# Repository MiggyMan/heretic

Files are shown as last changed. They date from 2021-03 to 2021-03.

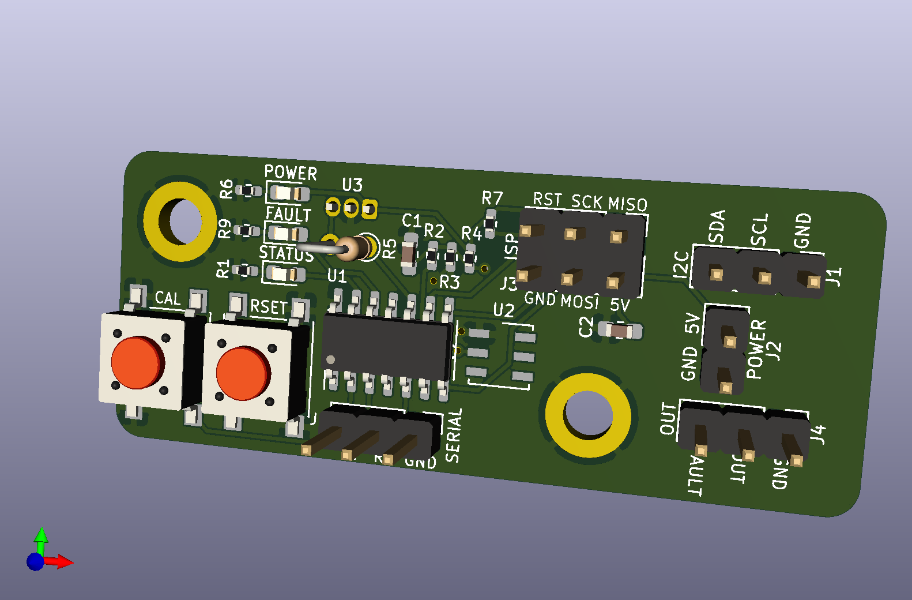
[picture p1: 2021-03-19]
electrical/kicad/filaSens-attiny84.png

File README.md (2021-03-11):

# heretic

My take on the infidel sensor

Forked from https://github.com/drspangle/infidel-sensor

# Original readme below

# Inline Filament Diameter Estimator, Lowcost (InFiDEL)

<p xmlns:dct="http://purl.org/dc/terms/" xmlns:vcard="http://www.w3.org/2001/vcard-rdf/3.0#">
  <a rel="license"
     href="http://creativecommons.org/publicdomain/zero/1.0/">
    
  </a>
  Originally created by Thomas Sanladerer
</p>

*A cheap, yet precise filament diameter sensor, intended to compensate for filament diameter deviations in real-time.*

The InFiDEL is a cheap (< $5) filament diameter sensor intended for use with FDM 3d printers.
The sensor can be calibrated to provide surprisingly precise filament diameter readings in real-time. 
The main idea is to use the sensor to correct for filament diameter deviations while printing.

Based on this proof-of-concept: https://www.youmagine.com/designs/filament-diameter-sensor

## Assembly and Setup
Assembly and Setup Instructions on Youtube (https://www.youtube.com/watch?v=RYgdLPe_T0c)

### Calibration
- Flash board with calibration.ino
- Connect a host via I2C (see provided host-example.ino)
- Insert each calibration drill bit shafts and replace the lookup table entries in driver.ino with your own measurements
  * Measure the actual diameter of the shafts and fill second column
  * Use the host's output *1000 to fill first column
- Finally, flash driver.ino with your values filled out
- Hub should now output exact diameter values

#### Note:
Analog output is currently not enabled in driver.ino (I2C and FAULT pin only)

## BOM

### Printed Parts
1 Block
1 Lever

#### Note:
Parts should preferably be printed in PETG, ABS or ASA as PLA may creep significantly over time.

### Electronics
There are two board variants included in this repository, either can be used to assemble the InFiDEL.

Choose one:
- SMT control board (which is populated; Gerber files and component specifications are included) 
- THT control board

Also required:

- Suitable programmer for ATTiny85 (eg USBtinyISP)
- 1 SS495A linear hall effect sensor (or comparable)

### Fasteners
- 2 M3x8 screws (eg ISO 4762 M2x8)
- 1 3x24mm pin (eg DIN 7 3x24mm, for mating lever to the block)
- 1 3x16mm pin (eg DIN 7 3x16mm, for roller bearing in lever)
- 1 3x18mm pin (eg DIN 7 3x18mm, for idler bearing in block)
- 6 M3 threaded inserts

Pins may be replaced with screws or grubscrews, which may result in decreased precision.

### Other Hardware
- 1 6x2mm magnet (eg N35)
- 4 623 bearings (preferably 623-2Z / 623-ZZ)
- 1 Ballpoint pen spring (or other soft 4mm spring)
- Short length of PTFE tube

### Calibration Accessories
- 1 1.5mm drill bit
- 1 1.7mm or 1.8mm drill bit 
- 1 2mm drill bit
- Calipers for verifying drill bit shaft diameter

Drill bits may be replaced with similar diameters. 
Measured diameter is to be written to firmware lookup table.

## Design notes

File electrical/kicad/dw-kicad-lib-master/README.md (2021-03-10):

# dw-kicad-lib
KiCad 5 symbol library

+ SS49X - Linear Hall-effect Sensor IC - SS490 Series (SS494B, SS495A, SS495A1, SS495A2, SS495B, SS496A, SS496A1, SS496B)

## Installation
For instructions on how to install/import please see this KiCad documentation.

## Licensing

The dw-kicad-lib is licensed under a CC-BY-SA 4.0 license (with an exception) so please see the LICENSE.md for more information.

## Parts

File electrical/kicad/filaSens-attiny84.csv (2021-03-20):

Comment | Designator | Footprint | LCSC
10uF | C1,C2 | Capacitor_SMD:C_0603_1608Metric_Pad1.05x0.95mm_HandSolder | C19702
STATUS | D1 | LED_SMD:LED_0603_1608Metric_Pad1.05x0.95mm_HandSolder | C72041
POWER | D2 | LED_SMD:LED_0603_1608Metric_Pad1.05x0.95mm_HandSolder | C72043
FAULT | D3 | LED_SMD:LED_0603_1608Metric_Pad1.05x0.95mm_HandSolder | C72038
MountingHole_Pad | H1,H2 | MountingHole:MountingHole_3.2mm_M3_ISO14580_Pad
I2C | J1 | Connector_PinHeader_2.54mm:PinHeader_1x03_P2.54mm_Vertical
POWER | J2 | Connector_PinHeader_2.54mm:PinHeader_1x02_P2.54mm_Vertical
ISP | J3 | Connector_PinHeader_2.54mm:PinHeader_2x03_P2.54mm_Vertical
OUT | J4 | Connector_PinHeader_2.54mm:PinHeader_1x03_P2.54mm_Vertical
SERIAL | J5 | Connector_PinHeader_2.54mm:PinHeader_1x03_P2.54mm_Vertical
1k | R1,R6,R9 | Resistor_SMD:R_0402_1005Metric_Pad0.72x0.64mm_HandSolder | C11702
36k | R2 | Resistor_SMD:R_0402_1005Metric_Pad0.72x0.64mm_HandSolder | C25783
9k1 | R3 | Resistor_SMD:R_0402_1005Metric_Pad0.72x0.64mm_HandSolder | C25926
18k | R4 | Resistor_SMD:R_0402_1005Metric_Pad0.72x0.64mm_HandSolder | C25762
4K7 | R5 | Resistor_THT:R_Axial_DIN0204_L3.6mm_D1.6mm_P2.54mm_Vertical | C25900
10k | R7 | Resistor_SMD:R_0402_1005Metric_Pad0.72x0.64mm_HandSolder | C25744
CAL | S1 | Button_Switch_SMD:SW_Push_1P1T_NO_6x6mm_H9.5mm | C127509
RSET | S2 | Button_Switch_SMD:SW_Push_1P1T_NO_6x6mm_H9.5mm | C127509
ATtiny84-20SSU | U1 | Package_SO:SOIC-14_3.9x8.7mm_P1.27mm | C144333
DS2431 | U2 | Package_SO_J-Lead:TSOC-6_3.76x3.94mm_P1.27mm | C9387
SS49X | U3 | Package_TO_SOT_THT:TO-92Flat

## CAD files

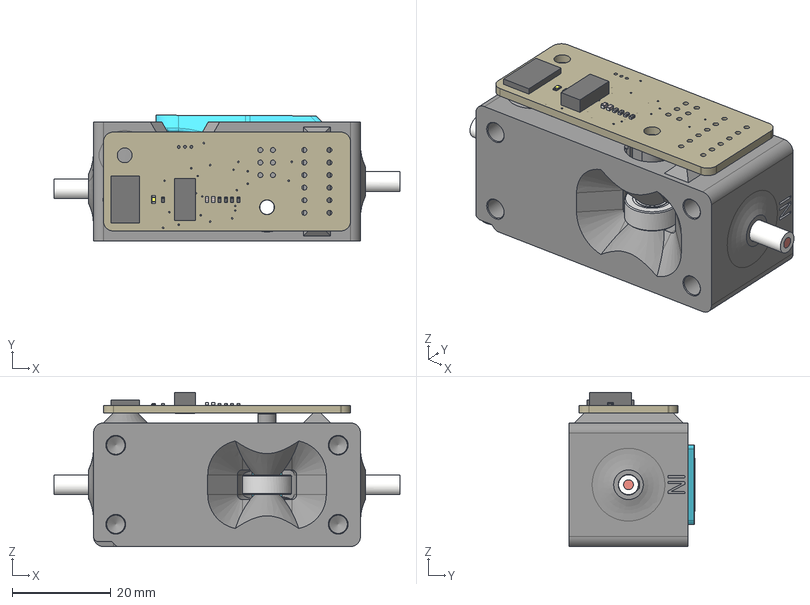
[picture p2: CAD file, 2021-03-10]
mechanical/InFiDEL_release.step
70.0 x 25.4 x 31.2 mm
LeverNew
7804K128 (1)
SpringPlunger
Filament
PTFE (1)
BlockClearance
Board
TACTILE_SWITCH_SMD_6.2MM_TALL
SIP3-UA
SOIC8
C0402 x 2
R0402 x 5

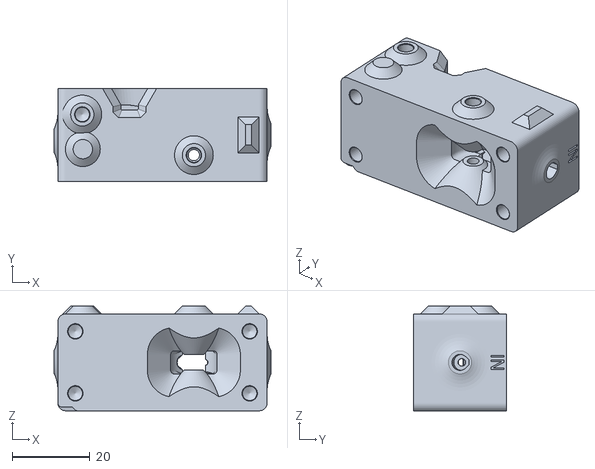
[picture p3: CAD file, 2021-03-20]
mechanical/stl/Block.stl
56.0 x 24.0 x 27.0

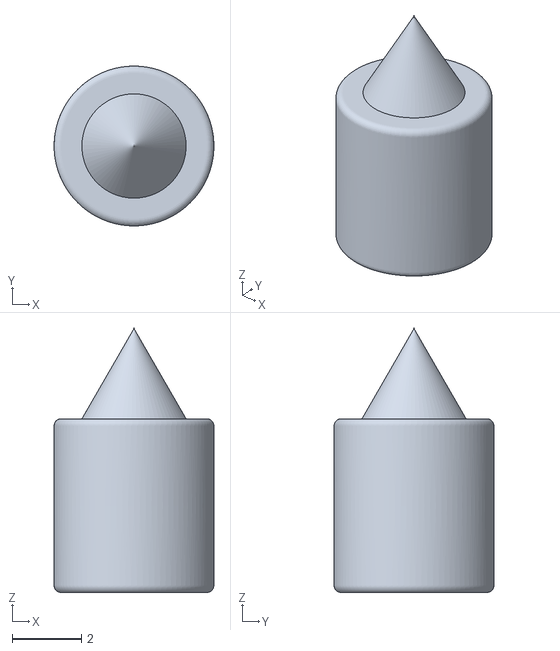
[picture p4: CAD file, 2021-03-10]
mechanical/stl/SpringPlunger.stl
4.60 x 4.60 x 7.60

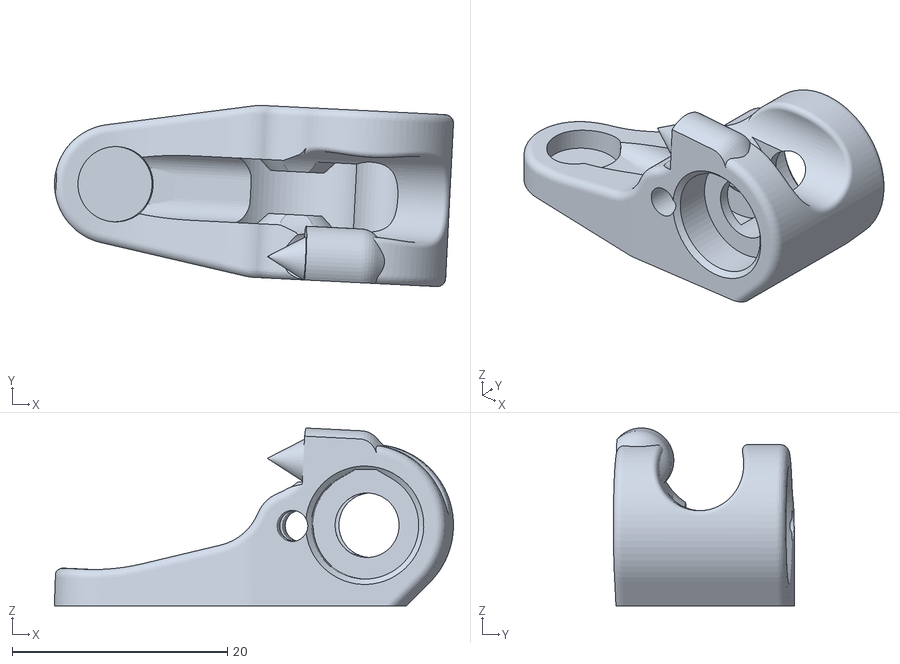
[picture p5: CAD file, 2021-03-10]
mechanical/stl/Lever.stl
37.1 x 16.8 x 16.5

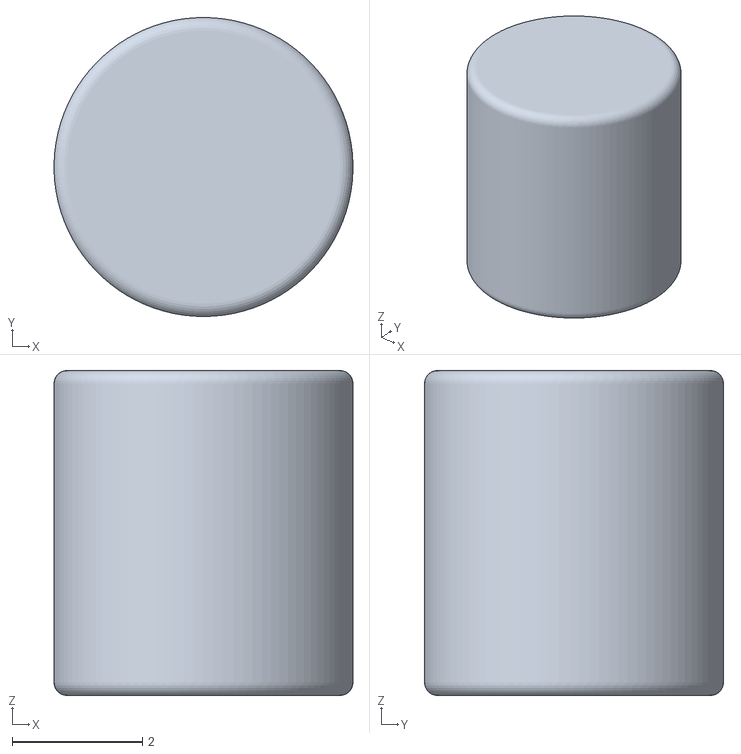
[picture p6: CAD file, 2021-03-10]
mechanical/stl/SpringPlungerExtender.stl
4.60 x 4.60 x 5.00

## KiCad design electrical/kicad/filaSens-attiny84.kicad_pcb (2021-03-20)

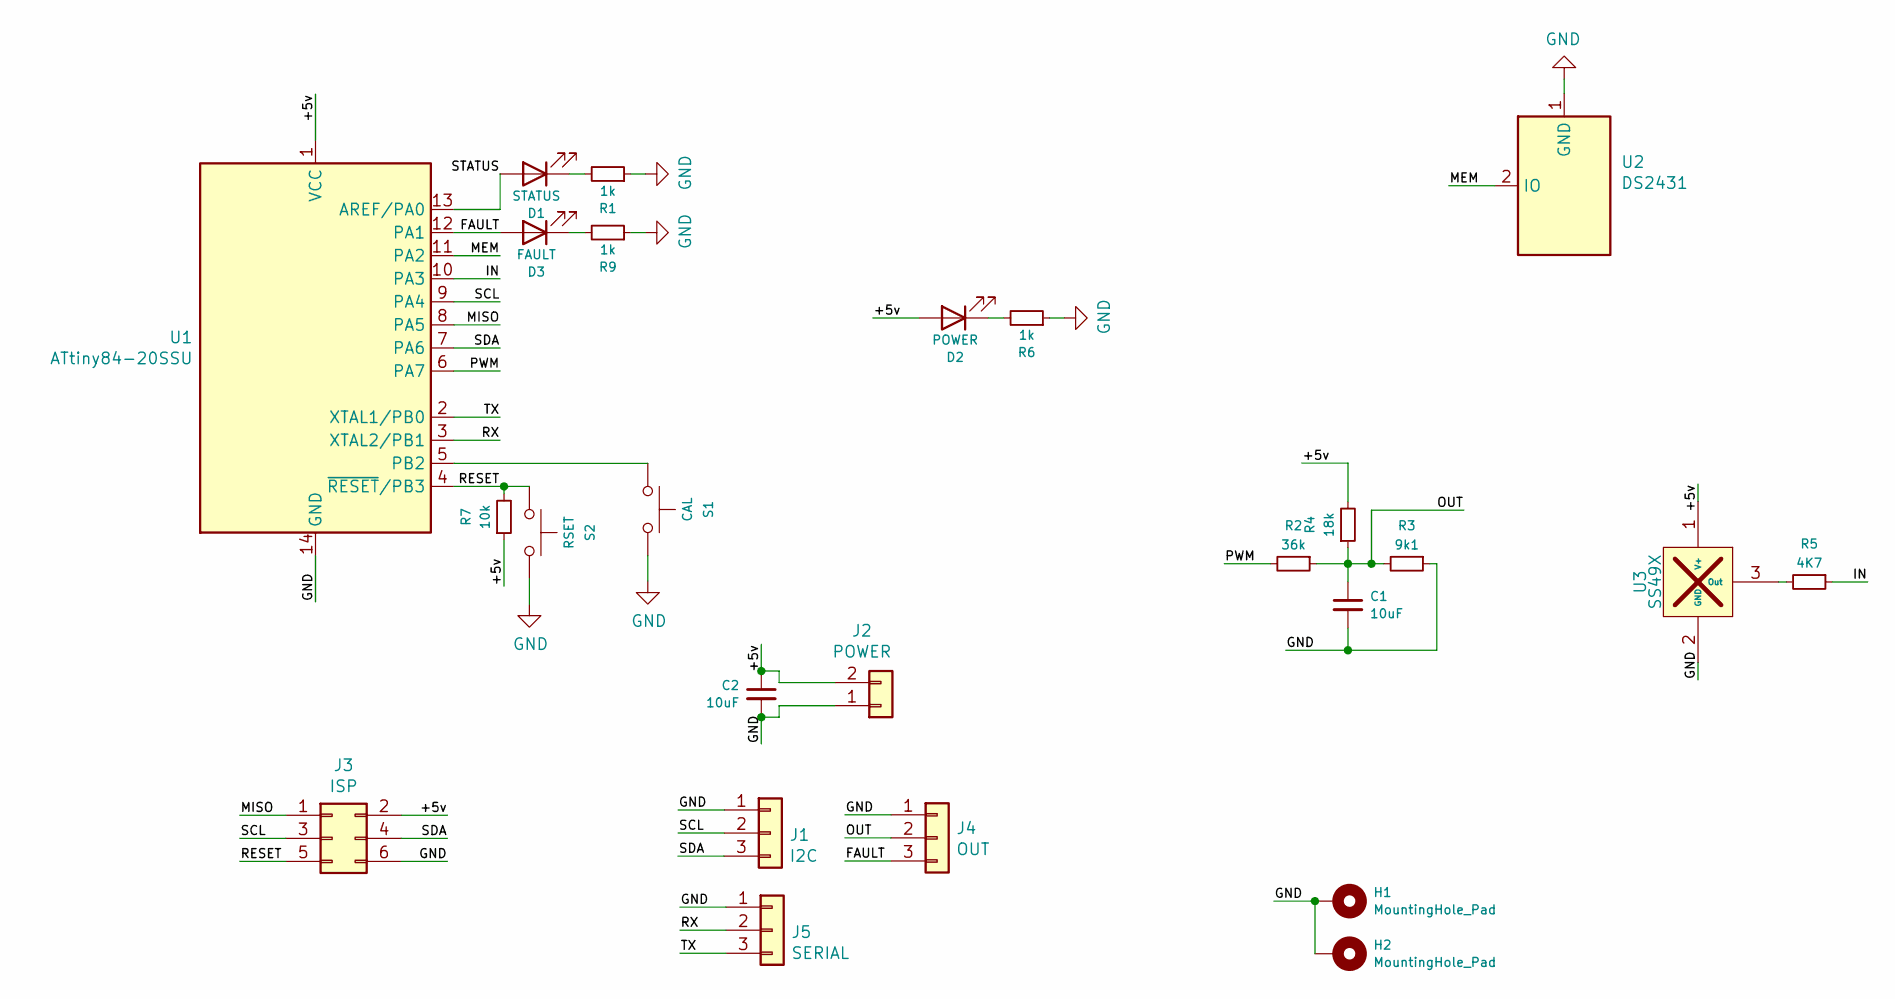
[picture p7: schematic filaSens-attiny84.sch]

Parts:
C1, C2: 10uF; C_0603_1608Metric_Pad1.05x0.95mm_HandSolder; LCSC C19702
D1: STATUS; LED_0603_1608Metric_Pad1.05x0.95mm_HandSolder; LCSC C72041
D2: POWER; LED_0603_1608Metric_Pad1.05x0.95mm_HandSolder; LCSC C72043
D3: FAULT; LED_0603_1608Metric_Pad1.05x0.95mm_HandSolder; LCSC C72038
H1, H2: MountingHole_Pad; MountingHole_3.2mm_M3_ISO14580_Pad
J1: I2C; PinHeader_1x03_P2.54mm_Vertical
J2: POWER; PinHeader_1x02_P2.54mm_Vertical
J3: ISP; PinHeader_2x03_P2.54mm_Vertical
J4: OUT; PinHeader_1x03_P2.54mm_Vertical
J5: SERIAL; PinHeader_1x03_P2.54mm_Vertical
R1, R6, R9: 1k; R_0402_1005Metric_Pad0.72x0.64mm_HandSolder; LCSC C11702
R2: 36k; R_0402_1005Metric_Pad0.72x0.64mm_HandSolder; LCSC C25783
R3: 9k1; R_0402_1005Metric_Pad0.72x0.64mm_HandSolder; LCSC C25926
R4: 18k; R_0402_1005Metric_Pad0.72x0.64mm_HandSolder; LCSC C25762
R5: 4K7; R_Axial_DIN0204_L3.6mm_D1.6mm_P2.54mm_Vertical; LCSC C25900
R7: 10k; R_0402_1005Metric_Pad0.72x0.64mm_HandSolder; LCSC C25744
S1: CAL; SW_Push_1P1T_NO_6x6mm_H9.5mm; LCSC C127509
S2: RSET; SW_Push_1P1T_NO_6x6mm_H9.5mm; LCSC C127509
U1: ATtiny84-20SSU; SOIC-14_3.9x8.7mm_P1.27mm; LCSC C144333
U2: DS2431; TSOC-6_3.76x3.94mm_P1.27mm; LCSC C9387
U3: SS49X; TO-92Flat

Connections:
/+5v: C2.1, D2.2 (A), J2.2, J3.2, R4.2, R7.1, U1.1 (VCC), U3.1 (V+)
/FAULT: D3.2 (A), J4.3, U1.12 (PA1)
/IN: R5.1, U1.10 (PA3)
/MEM: U1.11 (PA2), U2.2 (IO)
/MISO: J3.1, U1.8 (PA5)
/OUT: C1.1, J4.2, R2.1, R3.2, R4.1
/PWM: R2.2, U1.6 (PA7)
/RESET: J3.5, R7.2, S2.1, U1.4 (~RESET~/PB3)
/RX: J5.2, U1.3 (XTAL2/PB1)
/SCL: J1.2, J3.3, U1.9 (PA4)
/SDA: J1.3, J3.4, U1.7 (PA6)
/STATUS: D1.2 (A), U1.13 (AREF/PA0)
/TX: J5.3, U1.2 (XTAL1/PB0)
GND: C1.2, C2.2, H1.1, H2.1, J1.1, J2.1, J3.6, J4.1, J5.1, R1.1, R3.1, R6.1, R9.1, S1.2, S2.2, U1.14 (GND), U2.1 (GND), U3.2 (GND)
unnamed: D1.1 (K), R1.2
unnamed: D2.1 (K), R6.2
unnamed: D3.1 (K), R9.2
unnamed: R5.2, U3.3 (Out)
unnamed: S1.1, U1.5 (PB2)

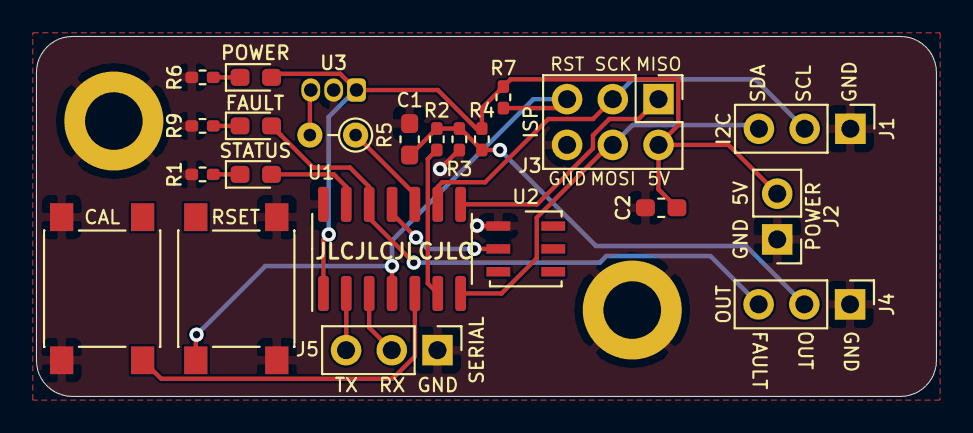
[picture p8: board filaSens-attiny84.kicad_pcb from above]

Board: 2 copper layers, 50.0 x 20.0 mm, 25 parts (0 on the bottom side), 19 nets.

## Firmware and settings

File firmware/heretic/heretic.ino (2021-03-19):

/*  Firmware for the **49* (eg SS495) hall-sensor based filament diameter sensor.
    Reads analog value from the sensor and provides a mapped and filtered diameter reading over I2C (optional analog output)

    Built for ATTiny85

    Upload firmware via programmer, using internal 16 MHz clock on ATTiny

    Compact filament sensor hardware and PCB: [URL]

    Licensed CC-0 / Public Domain by Thomas Sanladerer
*/
#include <elapsedMillis.h>

#define FaultLED 0 
#define StatusLED 10 
#define SensorPin 3
#define CalPin 8
#define PWMPin 7
#define sampleDelay 10
#define sampleTime 200
#define samples sampleTime/sampleDelay

// mode 0 i2c mode 1 serial
#define mode 1
  #include <Wire.h>
#if mode ==0
  #include <Wire.h>
  #define I2C_ADDR 43 //iterate for additional sensors in same I2C bus
#elif mode == 1
  #include <SoftwareSerial.h>
  //SoftwareSerial softSerial(4, 6);
  SoftwareSerial softSerial(1, 2);
#else
  #error No valid communication mode specified
#endif  

elapsedMillis avgTimer;
elapsedMillis sTimer;

#define smooth 100 //intensity of digital lowpass filtering

float dia = 0.0;
int sample=0;
int sampleSet[samples];
int average=0;

void setup() {
  //setup pins
  pinMode(FaultLED, OUTPUT);
  pinMode(StatusLED, OUTPUT);
  pinMode(SensorPin, INPUT);
  pinMode(CalPin, INPUT);
  pinMode(PWMPin, OUTPUT);

  //start I2C
  #if mode ==0
    Wire.begin(I2C_ADDR);
    Wire.onRequest(requestISR);
  #else
    Wire.begin();
    softSerial.begin(19200);
  #endif
  // Neeedless led flashing to show we're alive.
  digitalWrite(FaultLED, HIGH);
  digitalWrite(StatusLED, LOW);
  delay(250);
  digitalWrite(FaultLED, LOW);
  digitalWrite(StatusLED, HIGH);
  delay(250);
  digitalWrite(FaultLED, HIGH);
  digitalWrite(StatusLED, LOW);
  delay(250);
  digitalWrite(FaultLED, LOW);
  delay(50);
  digitalWrite(FaultLED, HIGH);
  digitalWrite(StatusLED, HIGH);
  delay(50);
  digitalWrite(FaultLED, LOW);
  digitalWrite(StatusLED, LOW);
  delay(50);
  digitalWrite(FaultLED, HIGH);
  digitalWrite(StatusLED, HIGH);
  delay(50);
  digitalWrite(FaultLED, LOW);
  digitalWrite(StatusLED, LOW);

  softSerial.println("Samples: "+String(samples));
  
}

void loop() {
  //get fresh reading
  if (sTimer >= sampleDelay ) {
    sTimer = 0;
    sampleSet[sample] = analogRead(SensorPin);
    sample++;
    if(avgTimer>sampleTime) {
      avgTimer=0;
      digitalWrite(StatusLED, HIGH);
      delay(50);
      digitalWrite(StatusLED, LOW);
      sample=0;
      average=0;
      for (int x = 0; x < samples; x++) {
        average = average + sampleSet[x];
      }
      average = average / samples;
      softSerial.println("Avg: "+String(average));
      dia = convert2dia(average) ;
      //light LED if sensor saturated (or button pressed)
      if (average < 3 or average > 1020) {
        digitalWrite(FaultLED, HIGH);
      }else {
        digitalWrite(FaultLED, LOW);
      }
    }else{
      softSerial.println("Sample: "+String(sampleSet[sample]));
    }
  }
}

#if mode ==0
void requestISR() {
  //sends smoothed diameter reading in um as two bytes via I2C
  //first byte is upper 8 bits, second byte lower 8 bits
  long senddia = 1000 * dia;
  byte b1 = floor(senddia / 256);
  byte b2 = (senddia % 256);
  Wire.write(b1);
  Wire.write(b2);
  //optional: Send raw reading for calibration
}
#endif

float convert2dia(float in) {
  //converts an ADC reading to diameter
  //Inspired by Sprinter / Marlin thermistor reading
  byte numtemps = 2;
  const float table[numtemps][2] = {
    //{ADC reading in, diameter out}

    //CALIBRATION ONLY
    //(unless you want to do the lookup on your host)
    
    { 0  , 0 },
    { 1023  , 1.023 }
  };
  byte i;
  float out;
  for (i = 1; i < numtemps; i++)
  {
    //check if we've found the appropriate row
    if (table[i][0] > in)
    {
      float slope = ((float)table[i][1] - table[i - 1][1]) / ((float)table[i][0] - table[i - 1][0]);
      float indiff = ((float)in - table[i - 1][0]);
      float outdiff = slope * indiff;
      float out = outdiff + table[i - 1][1];
      return (out);
      break;
    }
  }
}

void calibrate(){
 /*  TODO: Self-calibration
  *  Press button, insert 1mm brill bit shaft, press to confirm reading
  *  Repeat for 1.5mm, 1.7mm, 2mm
  *  (optional: use interpolated value based on point between 1.5 and 2mm if 1.7mm if read with implausible value
  */
}

void scanI2C() {
    byte error, address;
  int nDevices;
 
  softSerial.println("Scanning...");
 
  nDevices = 0;
  for(address = 1; address < 127; address++ )
  {
    // The i2c_scanner uses the return value of
    // the Write.endTransmisstion to see if
    // a device did acknowledge to the address.
    Wire.beginTransmission(address);
    error = Wire.endTransmission();
 
    if (error == 0)
    {
      Serial.print("I2C device found at address 0x");
      if (address<16)
        Serial.print("0");
      Serial.print(address,HEX);
      Serial.println("  !");
 
      nDevices++;
    }
    else if (error==4)
    {
      Serial.print("Unknown error at address 0x");
      if (address<16)
        Serial.print("0");
      Serial.println(address,HEX);
    }    
  }
  if (nDevices == 0)
    Serial.println("No I2C devices found\n");
  else
    Serial.println("done\n");
 
}

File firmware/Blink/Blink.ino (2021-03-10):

/*
  Blink

  Turns an LED on for one second, then off for one second, repeatedly.

  Most Arduinos have an on-board LED you can control. On the UNO, MEGA and ZERO
  it is attached to digital pin 13, on MKR1000 on pin 6. LED_BUILTIN is set to
  the correct LED pin independent of which board is used.
  If you want to know what pin the on-board LED is connected to on your Arduino
  model, check the Technical Specs of your board at:
  https://www.arduino.cc/en/Main/Products

  modified 8 May 2014
  by Scott Fitzgerald
  modified 2 Sep 2016
  by Arturo Guadalupi
  modified 8 Sep 2016
  by Colby Newman

  This example code is in the public domain.

  http://www.arduino.cc/en/Tutorial/Blink
*/

int LEDA=10;
int LEDB=0;

// the setup function runs once when you press reset or power the board
void setup() {
  // initialize digital pin LED_BUILTIN as an output.
  pinMode(LED_BUILTIN, OUTPUT);
}

// the loop function runs over and over again forever
void loop() {
  digitalWrite(LEDA, HIGH);   // turn the LED on (HIGH is the voltage level)
  digitalWrite(LEDB, LOW);
  delay(1000);                       // wait for a second
  digitalWrite(LEDA, LOW);    // turn the LED off by making the voltage LOW
  digitalWrite(LEDB, HIGH);
  delay(1000);                       // wait for a second
}

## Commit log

2021-03-10 Initial import, at this point only the electricalide of things differs.
    [Block.stl, InFiDEL_release.step, Lever.stl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]
2021-03-11 * Removed DS2402, twas a silly choice for a board with the option of being an i2c slave * Updated silkscreen for better readability * Added DS2431 one wire eeprom to replace the i2c one * Moved STATU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
    [filaSens-attiny84.kicad_pcb]
2021-03-19 * Split output headers into serial/i2c/analogue/power * Rearranged i2c/analouge/power headers to better fit horizontal pin headers * Made R5 throughole to make it easier to change and experiment with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
    [filaSens-attiny84.kicad_pcb, filaSens-attiny84.sch]
2021-03-20 * Updated the block model for v0.3 board layout * Updated gerbers, bom and placement files
    [Block.stl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]

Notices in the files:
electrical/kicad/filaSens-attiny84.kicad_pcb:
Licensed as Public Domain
